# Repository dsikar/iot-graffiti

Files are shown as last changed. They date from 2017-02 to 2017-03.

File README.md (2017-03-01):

# iot-graffiti

Cloud based graffiti artist  

Folder structure

-- arduino
-- cad
-- materials
-- web
-- wiki

## arduino  

Sketch for the NodeMCU  

## cad  

Autodesk Inventor cad files, .stls and g-code.

## materials

Bill of materials  

## web  

Web server files  

## wiki  

Github wiki 

Build for "The Cloud Challenge" CNBC series.

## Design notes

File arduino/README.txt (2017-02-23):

The Arduino sketch folder, created by default once sketch is saved.

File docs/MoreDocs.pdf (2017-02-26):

NodeMCU configuration procedure

1. In Arduino IDE load sketch:

https://raw.githubusercontent.com/dsikar/iot-graffiti/master/arduino/iot-graffiti/iot-graffiti.ino

2. Edit network SSID and password in void setup() e.g.

WiFiMulti.addAP("Makerversity_2G", "mak3rv3rs1ty");

3. Edit http request address (in case server is not responding) in void loop() e.g.

String httpReq = "http://34.251.26.97/graffiti.php";

4. Connect NodeMCU board with USB micro cable.
5. Select Tools > Board > NodeMCU 1.0 (ESP-12 Module)
6. Select Tools > Port > (COM Port) *beware of other USB devices*
7. Upload sketch to NodeMCU (CTRL+U).
8. Remove USB Cable and power NodeMCU with jumper wire from breadboard to pin VIN (bottom left).

Web access

Access canvas.php on the same IP address as configured in NodeMCU e.g.

http://34.251.26.97/canvas.php

Start up procedure

1. Reset NodeMCU (reset button to left of USB connector).
2. Ajust weight heights as per photo:

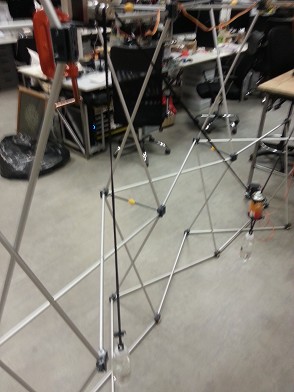
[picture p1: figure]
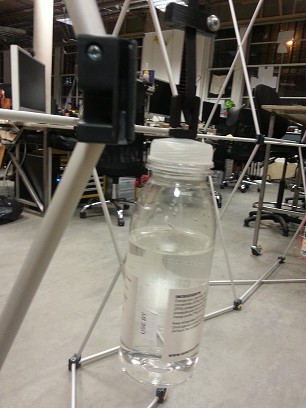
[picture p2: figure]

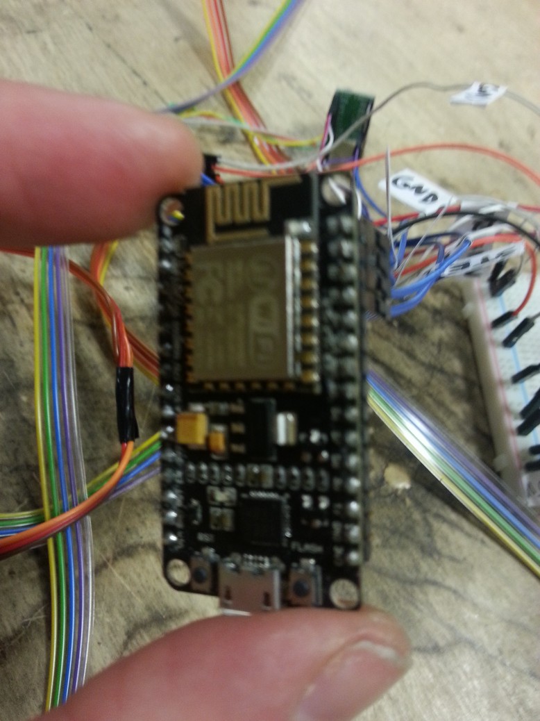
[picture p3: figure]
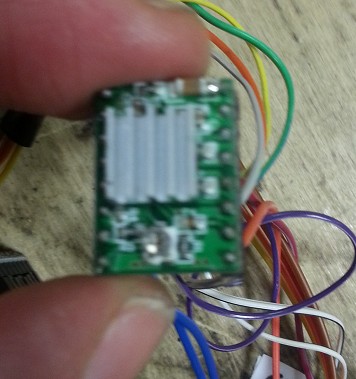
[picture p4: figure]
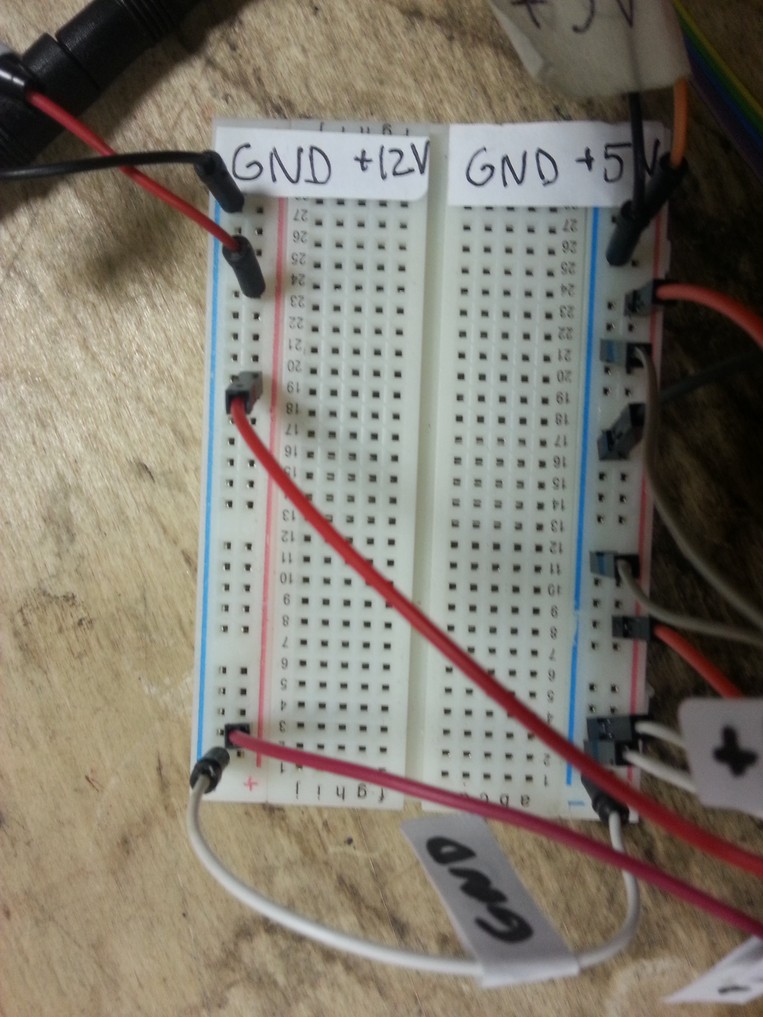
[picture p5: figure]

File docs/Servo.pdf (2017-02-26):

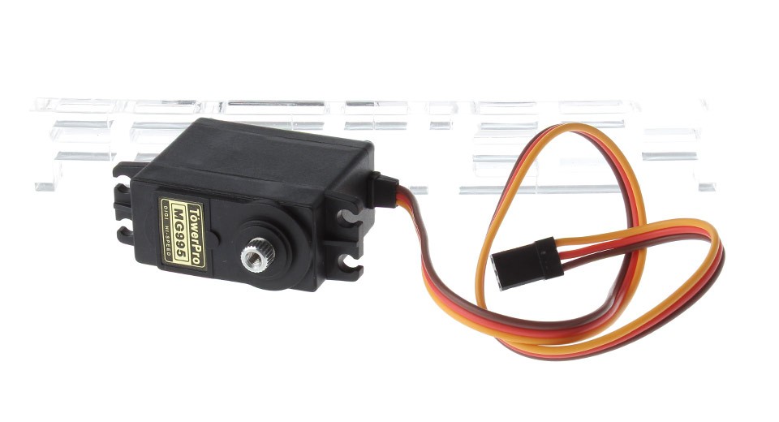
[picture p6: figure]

BROWN – GND
RED - +5V
ORANGE - D4 (NodeMCU)

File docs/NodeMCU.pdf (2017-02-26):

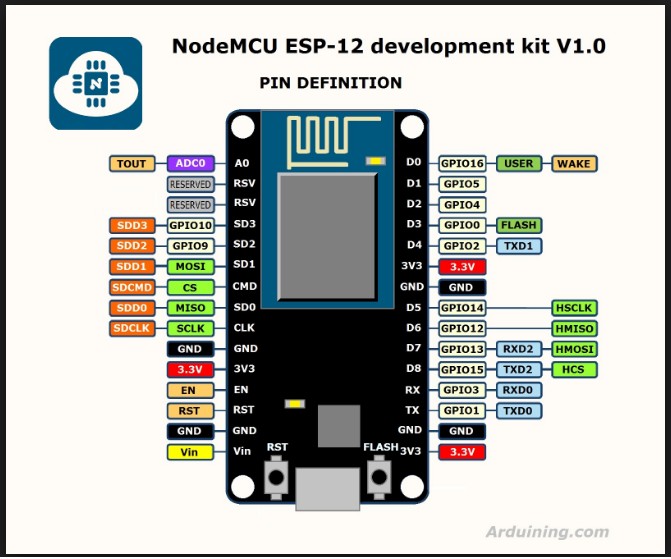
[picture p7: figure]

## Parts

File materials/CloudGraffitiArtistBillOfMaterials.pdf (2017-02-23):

## Cloud Graffiti Articulated Arm CNBC The Cloud Challenge

## Bill of Materials

Item | Quantity Supplier | Notes

## HARDWARE

Nema 17 Stepper Motor | 2 | http://ebay.eu/2fX6YXQ
M4 / 16mm / 100 | 1 | Thread Diameter M4 / Bolt Length 16mm / Your pack quantity 100
M4 Nut (100 pack) | 1 pack | http://bit.ly/2gbuI9C
M4 Washer (100 pack) | 1 pack | http://bit.ly/2fiGLxe

## ELECTRONICS

NodeMCU Module (£5.99) | 2 | http://ebay.eu/2dPgrfW
Stepstick | 4 | http://ebay.eu/2eZSn90

## CONSUMABLES

PLA Filament 2.85mm | 1 | http://bit.ly/2frAPDh
3.2mm plywood (RW20027) | 1 | http://bit.ly/2g5YEVK

http://www.ebay.co.uk/itm/121766702906

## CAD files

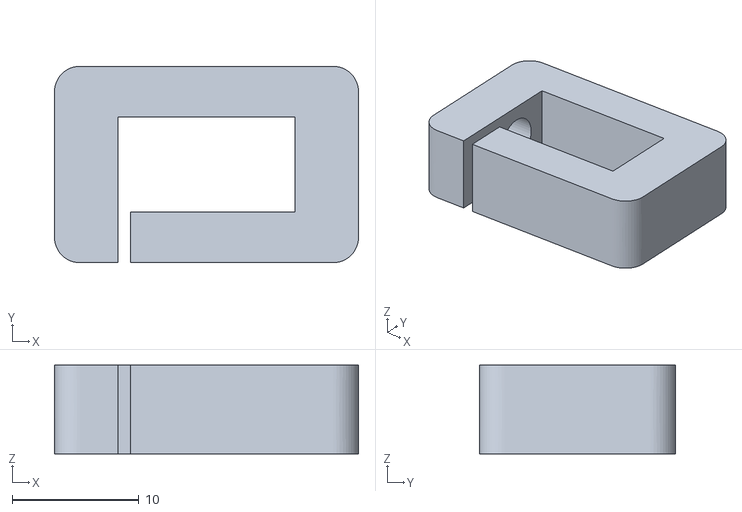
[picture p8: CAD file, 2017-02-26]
cad/stl/CounterWeightHook.stl
24.0 x 15.5 x 7.00

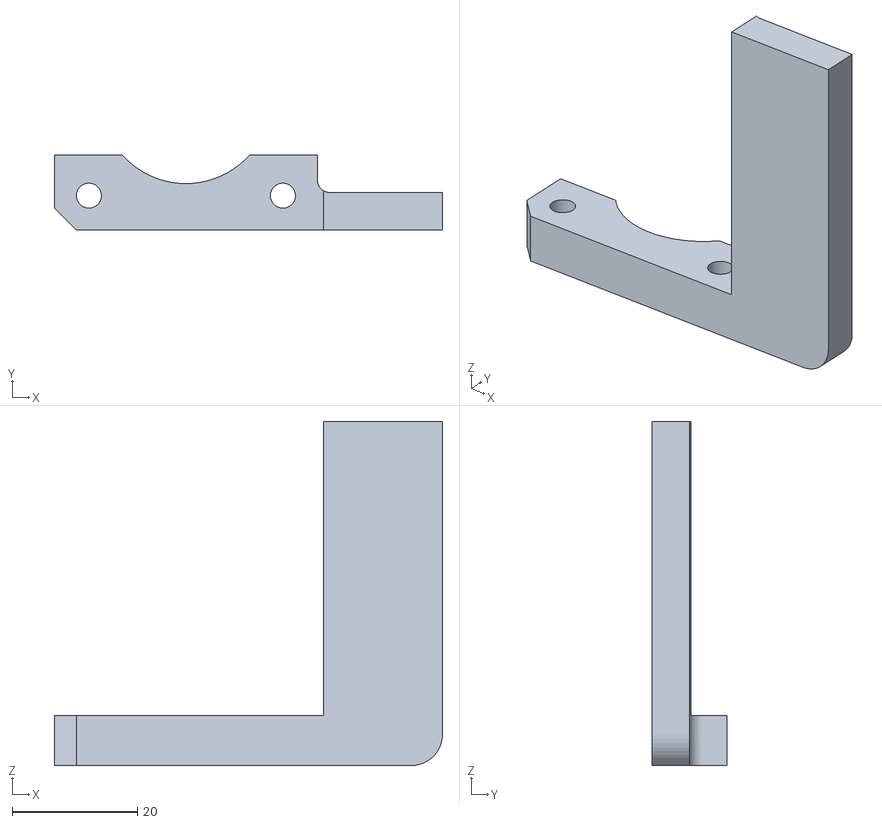
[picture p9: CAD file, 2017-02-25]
cad/stl/LeftBracket.stl
62.0 x 12.0 x 55.0

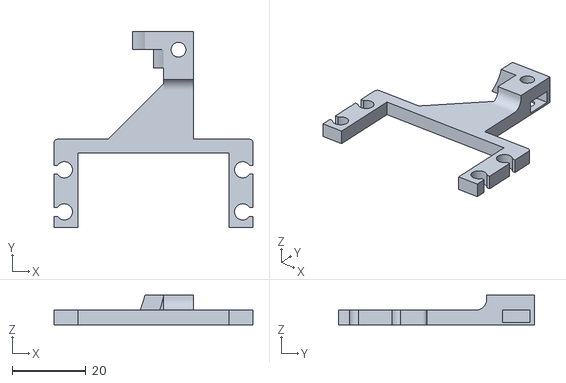
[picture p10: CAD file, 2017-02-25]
cad/stl/ExtendedBracket.stl
53.9 x 53.2 x 8.10

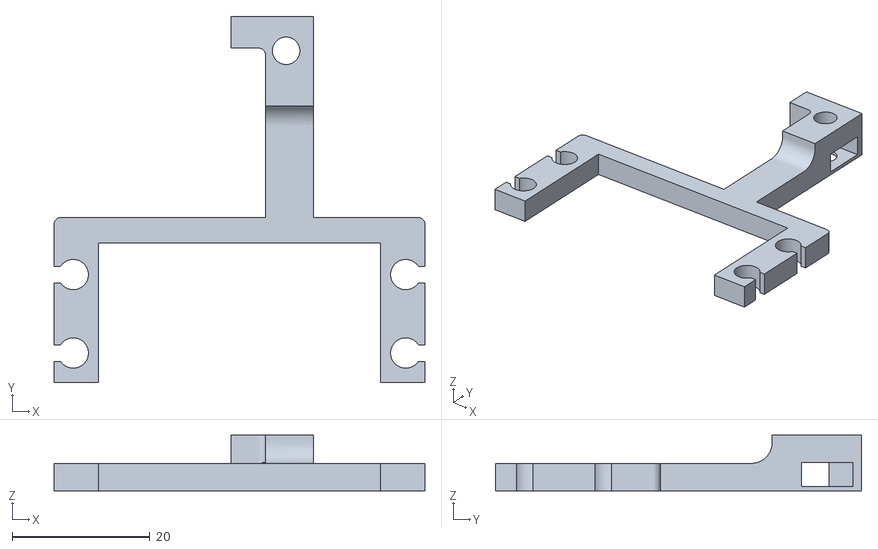
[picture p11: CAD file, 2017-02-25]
cad/stl/MG996RExtendedBracket.stl
53.9 x 53.2 x 8.10

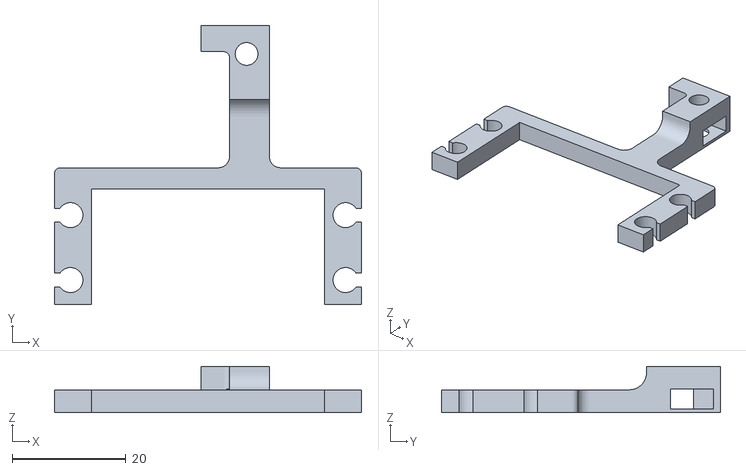
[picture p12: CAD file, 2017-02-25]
cad/stl/MG996RBracket.stl
53.9 x 49.0 x 8.10

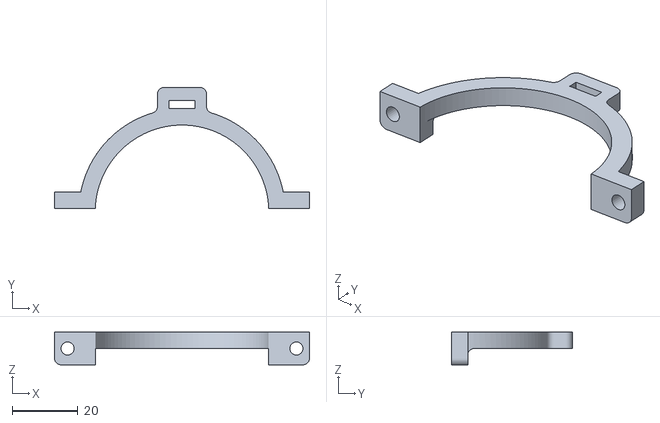
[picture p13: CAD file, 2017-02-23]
cad/stl/CanBracket.stl
77.8 x 37.0 x 10.0

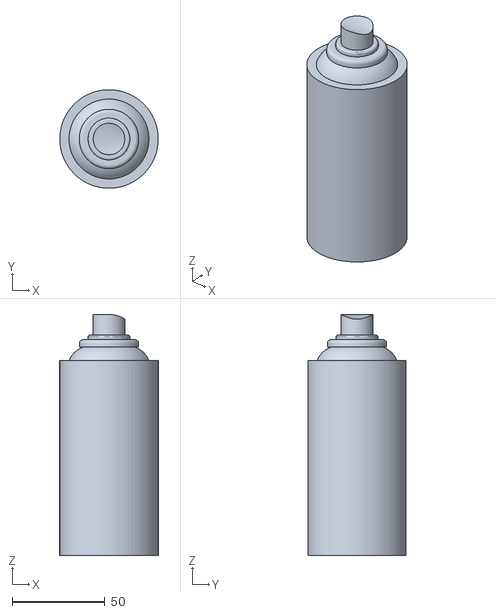
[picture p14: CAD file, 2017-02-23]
cad/stl/SprayCan105mm.stl
53.0 x 53.0 x 129.7

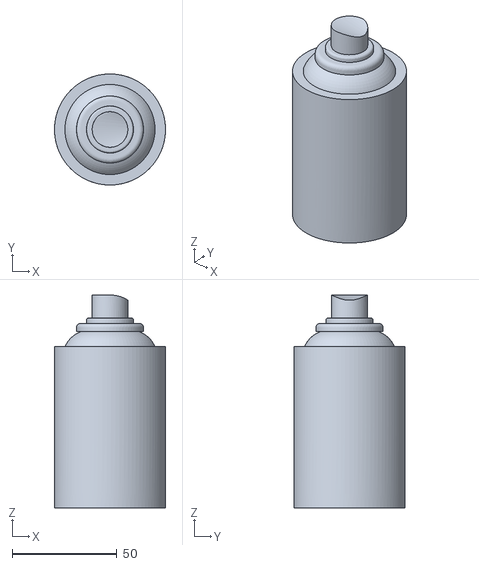
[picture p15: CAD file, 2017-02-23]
cad/stl/SprayCan77mm.stl
53.0 x 53.0 x 101.7

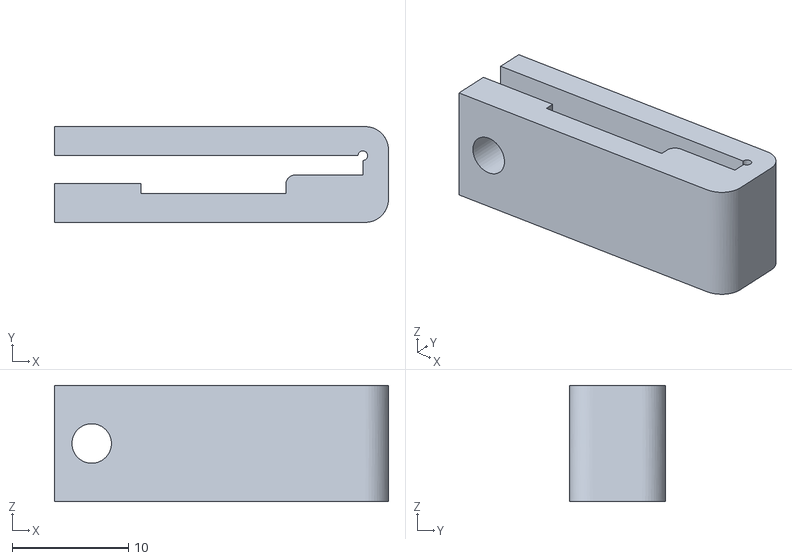
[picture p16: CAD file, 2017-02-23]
cad/stl/Loop.stl
28.7 x 8.24 x 10.0

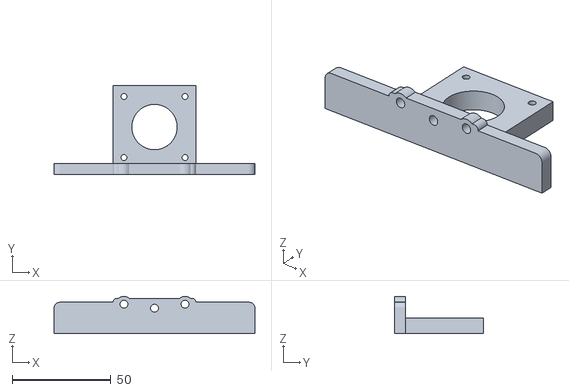
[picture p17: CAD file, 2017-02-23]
cad/stl/StepperMotorPlate.stl
102.0 x 45.0 x 19.0

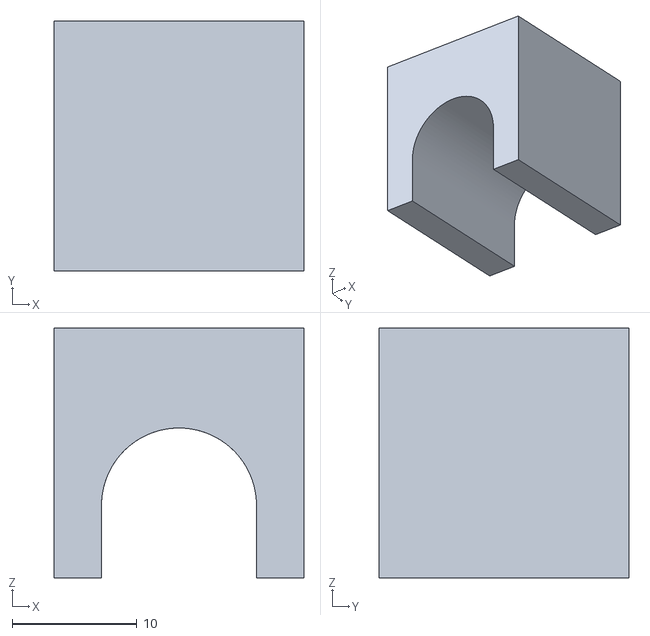
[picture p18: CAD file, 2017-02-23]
cad/stl/SupportBlock.stl
20.0 x 20.0 x 20.0

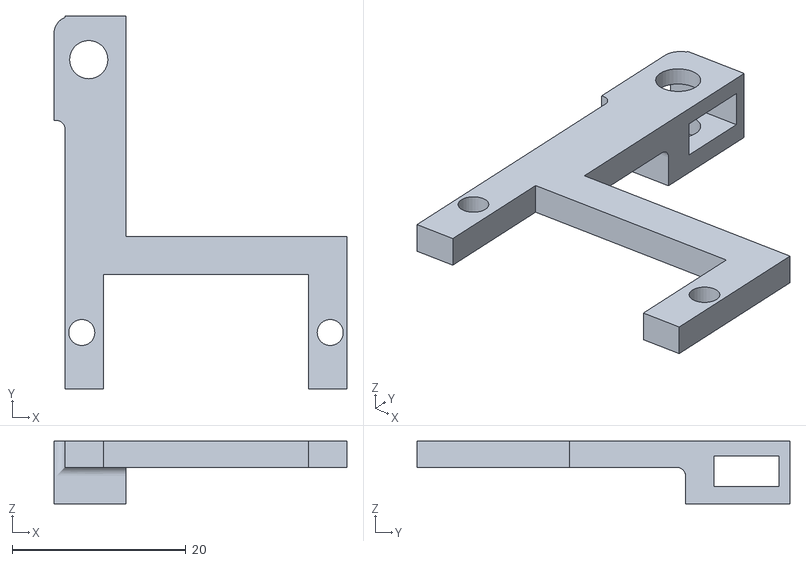
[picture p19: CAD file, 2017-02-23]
cad/stl/ServoBracket.stl
33.7 x 42.9 x 7.20

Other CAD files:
cad/stl/RightBracket.stl
cad/assemblies/ExtendedBracket.iam
cad/assemblies/Gears.iam
cad/assemblies/OldVersions/ServoAndHorn.0001.iam
cad/assemblies/ServoAndHorn.iam
cad/assemblies/SprayCanAndServo.iam
cad/drawings/CloudGraffitiPlotterRig.idw
cad/drawings/OldVersions/CloudGraffitiPlotterRig.0001.idw
cad/parts/CanBracket.ipt
cad/parts/CloudGraffitiPlotterRig.ipt
cad/parts/CounterWeightHook.ipt
cad/parts/CounterWeightLoop2.ipt
cad/parts/LeftBracket.ipt
cad/parts/Loop.ipt
cad/parts/MG996RBracket.ipt
cad/parts/MG996RBracketBottom.ipt
cad/parts/MG996RBracketTop.ipt
cad/parts/NEMA17StepperMotor.ipt
cad/parts/RightBracket.ipt
cad/parts/ServoBracket.ipt
cad/parts/SprayCan.ipt
cad/parts/SprayCan105mm.ipt
cad/parts/SprayCan77mm.ipt
cad/parts/StepperMotorPlate.ipt
cad/parts/SupportBlock.ipt

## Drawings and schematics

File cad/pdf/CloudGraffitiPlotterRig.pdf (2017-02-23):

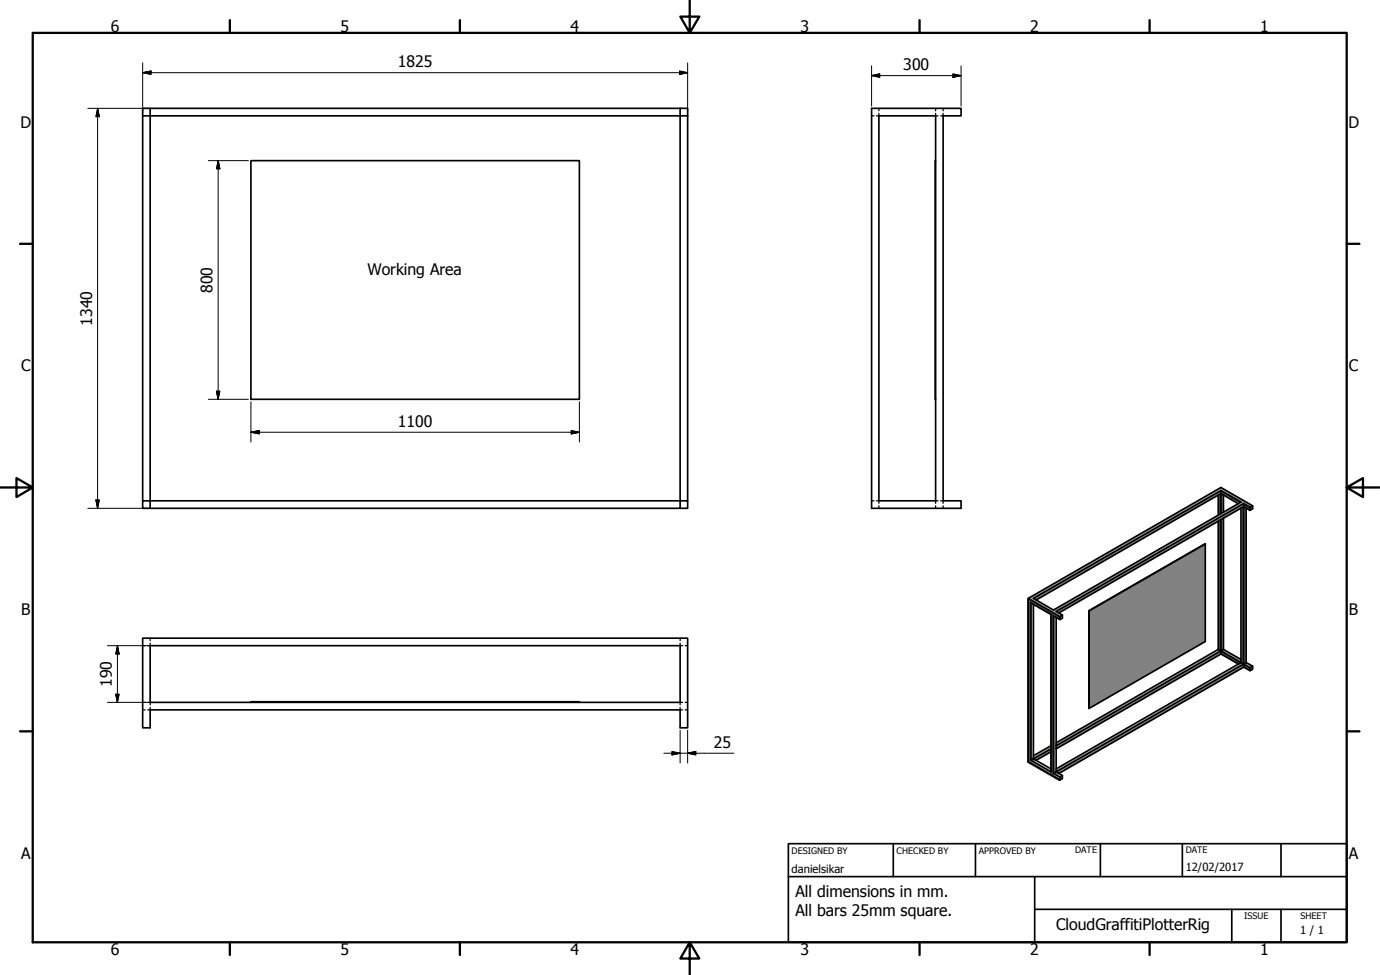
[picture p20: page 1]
CloudGraffitiPlotterRig; DESIGNED BY; CHECKED BY; APPROVED BY; DATE; danielsikar; ISSUE; SHEET; Working Area

All dimensions in mm.
All bars 25mm square.

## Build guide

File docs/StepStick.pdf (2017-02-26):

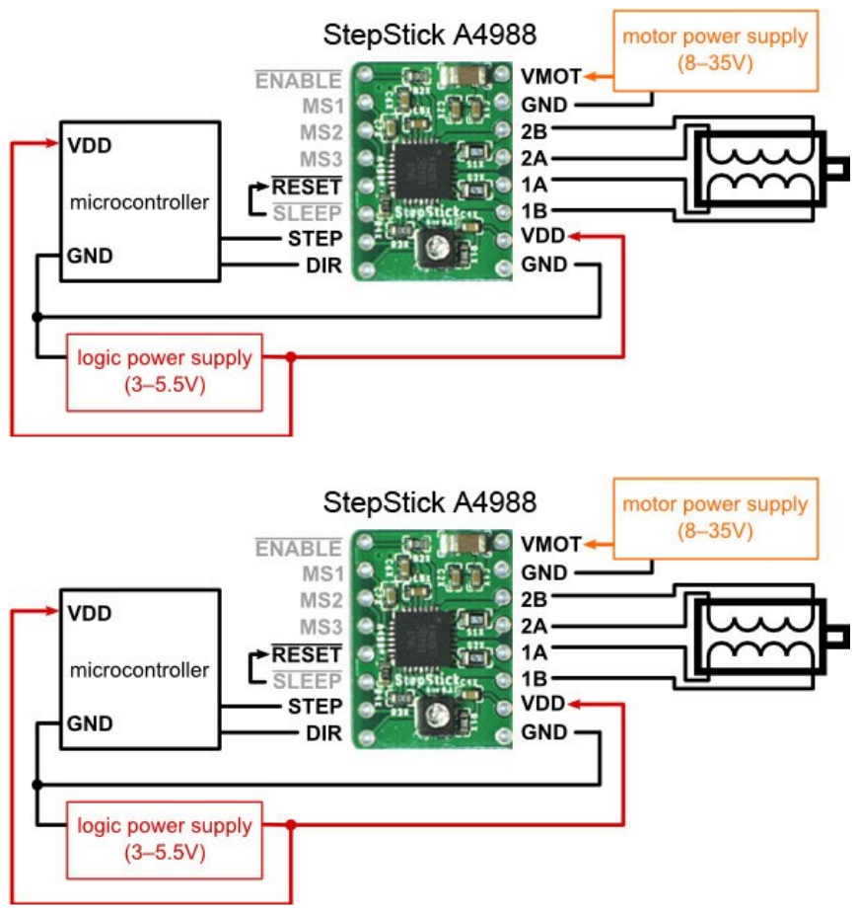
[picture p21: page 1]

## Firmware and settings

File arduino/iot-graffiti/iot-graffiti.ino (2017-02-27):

/**
 * CloudGraffitiPlotter
 *
 *  Created on: 21.02.2017
 *
 */
 
 // Changes required
 // 1. SSID and Password
 // 2. IP Address of AWS IOT-Trike server


#include <Arduino.h>
#include <Servo.h> 

// ESP8266 includes
#include <ESP8266WiFi.h>
#include <ESP8266WiFiMulti.h>
#include <ESP8266HTTPClient.h>
#define USE_SERIAL Serial
ESP8266WiFiMulti WiFiMulti;

// Graffiti-able area constants in mm
#define iXLength 1310
#define iYLength 800
// margins
#define iMarginX 150 
#define iMarginY 150
// initial XY positions
#define iInitX 550
#define iInitY 400

// Delimiter character for move commands
String strDelim = "|";

// Serial debug. Set to 1 to debug.
#define SERIAL_DEBUG 0
#define SERIAL_DEBUG_2 0
// Servo objects
Servo sprayServo;
// Servo pins
int sprayPin = 2; // D4

// Stepper pins
int iDirX = 16; // D0
int iStepX = 5; // D1
int iDirY = 4; // D2
int iStepY = 0; // D3

// Stepper step delay (less delay = faster)
int iStepDelay = 2;
// Serial parsing string
String txtMsg;
// Stepper motor move positions
int cnt;
int iH;
int iV;
int iNextPosX = 0; // or initial position e.g. 50
int iNextPosY = 0; // or initial position e.g. 50

// Current Position - TODO SET in setup();
int iCurrPosX = 1100; //cm
int iCurrPosY = 1100; //cm

// multiplier ~ turn mm into steps
// int iCoordMult = 47; // (46.94836 steps move 1cm)
float fCoordMult = 4.7; // steps to move 1mm

// Http delay - how often to pool web page
int iHttpDelay = 50;

void setup() {

    pinMode(iDirX, OUTPUT);
    pinMode(iStepX, OUTPUT);
    pinMode(iDirY, OUTPUT);
    pinMode(iStepY, OUTPUT);
  
    sprayServo.attach(sprayPin);
    // switch off
    sprayOff(sprayServo);
 
 
    // ESP8266 init routines
    USE_SERIAL.begin(115200);
    // USE_SERIAL.setDebugOutput(true);

    USE_SERIAL.println();
    USE_SERIAL.println();
    USE_SERIAL.println();

    for(uint8_t t = 4; t > 0; t--) {
        USE_SERIAL.printf("[SETUP] WAIT %d...\n", t);
        USE_SERIAL.flush();
        delay(3000);
    }

    // Commented out for debugging - COMMENT IN ONCE WORKING
    //WiFiMulti.addAP("zuzunet", "t3rr1v3l!");
    // WiFiMulti.addAP("BTHub6-Z2R7", "HYp7rXgi4Hxm");
    // WiFiMulti.addAP("TP-LINK_C8F400", "80552109");
    WiFiMulti.addAP("Makerversity_2G", "mak3rv3rs1ty");
    // WiFiMulti.addAP("South London Makerspace", "portugal");
    // WiFiMulti.addAP("SKYFF71E", "ARUPSXSY");
}

void initSteppers() {
  setHigh(iDirX);
  setHigh(iDirY);
}

void setHigh(int iPin) {
  digitalWrite(iPin, HIGH);
}

void setLow(int iPin) {
  digitalWrite(iPin, LOW);
}

void loop() {
    
    // wait for WiFi connection
    if((WiFiMulti.run() == WL_CONNECTED)) {

        HTTPClient http;

        USE_SERIAL.print("[HTTP] begin...\n");
        // configure traged server and url

        String httpReq = "http://34.251.26.97/graffiti.php";
        http.begin(httpReq);

        USE_SERIAL.print("[HTTP] GET...\n");
        // start connection and send HTTP header
        int httpCode = http.GET();
        USE_SERIAL.println("httpCode = ");
        USE_SERIAL.println(httpCode);
        USE_SERIAL.println("HTTP_CODE_OK = ");
        USE_SERIAL.println(HTTP_CODE_OK);
        // httpCode will be negative on error
        if(httpCode > 0) {
            // HTTP header has been send and Server response header has been handled
            //USE_SERIAL.printf("[HTTP] GET... code: %d\n", httpCode);
            // file found at server
            if(httpCode == HTTP_CODE_OK) {
                String payload = http.getString();
                USE_SERIAL.println(payload);
                parse(payload);
            }
        } else {
            USE_SERIAL.printf("[HTTP] GET... failed, error: %s\n", http.errorToString(httpCode).c_str());
        }
        http.end();
    } 
    delay(iHttpDelay);
}

void sprayOn(Servo myServo) {
  /*
  int pos;
  for(pos = 0; pos <= 90; pos += 1) // goes from 0 degrees to 180 degrees 
  {                                  // in steps of 1 degree 
    myServo.write(pos);              // tell servo to go to position in variable 'pos' 
    delay(15);                       // waits 15ms for the servo to reach the position 
  } 
  */
  int pos = 0;
  myServo.write(pos);
  delay(15);
}

void sprayOff(Servo myServo) {
  /*
  int pos;
  for(pos = 90; pos>=0; pos-=1)     // goes from 180 degrees to 0 degrees 
  {                                
    myServo.write(pos);              // tell servo to go to position in variable 'pos' 
    delay(15);                       // waits 15ms for the servo to reach the position 
  } 
  */
  int pos = 65;
  myServo.write(pos);
  delay(15);
}

/*******************

FUNCTIONS

*******************/

/*
  parse - parse message and send to be processed
*/

void parse(String strGraffiti) {
  if(SERIAL_DEBUG) {
    USE_SERIAL.println(strGraffiti);
  }
  
  if(isMove(strGraffiti)) {
    getSetXY(strGraffiti); 
  }
}

bool isMove(String strGraffiti) {
  // expected move format "xx|yy|spray_state"
  int iDelimCount = 0;
  int iStrLength = strGraffiti.length();
  
  for (int i=0; i < iStrLength; i++) {
    if(strGraffiti.substring(i, i+1) == strDelim) {
       iDelimCount++;
    } 
  } 
  if(iDelimCount==2) {
    return true;
  }
  return false;
}

/*
  getSetXY values and move if need be
*/

void getSetXY(String strGraffiti) {
  // format is XX|YY|(1|0), parse
  strGraffiti.trim(); // remove end of line character
  
  int iStart = 0;
  int iEnd = strGraffiti.indexOf(strDelim);
  String strX = strGraffiti.substring(iStart, iEnd);
  int iX = strX.toInt();
  iStart = iEnd + 1;
  iEnd = strGraffiti.indexOf(strDelim, iStart);
  String strY = strGraffiti.substring(iStart, iEnd);
  int iY = strY.toInt();
  iStart = iEnd + 1;
  iEnd = strGraffiti.length();
  String strSpray = strGraffiti.substring(iStart, iEnd);
  int iSpray = strSpray.toInt();
  
  if(SERIAL_DEBUG) {
    USE_SERIAL.print("strX = *");
    USE_SERIAL.print(strX);
    USE_SERIAL.println("*");    
    USE_SERIAL.print("strY = *");
    USE_SERIAL.print(strY);
    USE_SERIAL.println("*");     
    USE_SERIAL.print("strSpray = *");
    USE_SERIAL.print(strSpray); 
    
    USE_SERIAL.println("*");
    USE_SERIAL.print("iX = *");
    USE_SERIAL.print(iX);
    USE_SERIAL.println("*");    
    USE_SERIAL.print("iY = *");
    USE_SERIAL.print(iY);
    USE_SERIAL.println("*");     
    USE_SERIAL.print("iSpray = *");
    USE_SERIAL.print(iSpray); 
    USE_SERIAL.println("*");       
  }
  
  setPos(iX, iY, iSpray);
  
}

/*
  setPos - set x and y timing belt lengths
*/

void setPos(int iX, int iY, int iSpray) {

  // Origin (0,0) set at top left.
  // Mirror to top right if canvas is mounted on
  // a wall - spraying against wall
  // Do not mirror is canvas is mounted on rig -
  // spraying against rig

  // if we are spraying
  if(iSpray) {
   
    // move sqrt to cloud, perfoming poorly on embedded CPU
    // int iHypX = getHypX(iX, iY);
    // int iHypY  = getHypY(iX, iY);
 
    // position spray can only deal with x for now
    windX(iX);
    windY(iY);
    
    // press spray
    sprayOn(sprayServo);
  }
  else {
    // release spray
    // don't bother moving
    sprayOff(sprayServo);
  }
}

void windX(int iX) {
    if(SERIAL_DEBUG) {
      USE_SERIAL.print("windX(int iX)");
    }
      
  int iMove = iX - iCurrPosX;
   if(SERIAL_DEBUG) {
    USE_SERIAL.print("iMove = ");
    USE_SERIAL.println(iMove);
    USE_SERIAL.print("abs(iX - iCurrPosX) = ");
    USE_SERIAL.println(abs(iX - iCurrPosX)); 
  }
  // NB Inverted logic for X
  if(iMove > 0) {
    if(SERIAL_DEBUG) {
      USE_SERIAL.print("setHigh(iDirX)"); 
    }     
    // setLow(iDirX);
    setHigh(iDirX);
  } else {
    if(SERIAL_DEBUG) {
      USE_SERIAL.print("setLow(iDirX)"); 
    }     
    // setHigh(iDirX);
    setLow(iDirX);
  }
  float fTotalSteps = abs(iMove) * fCoordMult;
  int iTotalSteps = fTotalSteps;
   if(SERIAL_DEBUG) {
    USE_SERIAL.print("iTotalSteps = ");
    USE_SERIAL.println(iTotalSteps);
   }  
  for(int i = 0; i <= iTotalSteps; i++) {
    oneStep(iStepX);
  }
  // keep track of where we are
  iCurrPosX = abs(iX);
  if(SERIAL_DEBUG) {
    USE_SERIAL.print("iCurrPosX = ");
    USE_SERIAL.println(iCurrPosX);
  }   
}

void windY(int iY) {
  int iMove = iY - iCurrPosY;  
  if(iMove > 0) {
    // setHigh(iDirY);
    setLow(iDirY);
  } else {
    // setLow(iDirY);
    setHigh(iDirY);
  }
  float fTotalSteps = abs(iMove) *  fCoordMult;
  int iTotalSteps = fTotalSteps;
  for(int i = 0; i <= iTotalSteps; i++) {
    oneStep(iStepY);
  }
  // keep track of where we are
  iCurrPosY = abs(iY);
}

void oneStep(int iStepPin) {
    digitalWrite(iStepPin, HIGH);
    delay(iStepDelay);
    digitalWrite(iStepPin, LOW);
    delay(iStepDelay);  
}

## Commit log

2017-02-23 Initial commit.
    [CanBracket.ipt, CanBracket.stl, CloudGraffiti.ods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]
2017-02-25 New directory structure.
    [CounterWeightHook.ipt, CounterWeightHook.stl, ExtendedBracket.iam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]
2017-02-25 Added hook.
    [CounterWeightHook.ipt, CounterWeightHook.stl]
2017-02-26 Inverted spray on off logic.
    [iot-graffiti.ino]
